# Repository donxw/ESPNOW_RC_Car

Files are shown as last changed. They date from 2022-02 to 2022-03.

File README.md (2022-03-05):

# ESPNOW_RC_Car
SMARS inspired RC Car using ESPNOW to transmit signals from the remote control unit.

*Chassis_V2 v5.f3z*

SMARS_Front2 (Small)

SMARS_Front (Small)

## Credits
This project was inspired by the SMARS arduino car described at this website:  https://www.smarsfan.com/ 

Modifications were made to use ESP based microcontrollers for RC wireless signal communication using the ESPNOW protocol. This minimized any addtional hardware by using the built in wireless capabilities of the ESP boards.  

Additionally, the wheels were redesigned to use an o-ring in place of the 3D printed tank treads.

## Libraries Used
espnow.h - here is the tutorial I used:  https://randomnerdtutorials.com/esp-now-esp8266-nodemcu-arduino-ide/
The car uses the ESP8266 commands and the Remote Control uses the ESP32 commands

No library is needed for the NodeMCU motor driver board.  The motor driver is an L293D controlled as follows:

*Motor A*
*   Direction A - Pin 0 (D3) - Boolean 0 or 1 to change direction
*   PWM A - Pin 5 (D1) - PWM 0-255 for speed

*Motor B*
*   Direction B - Pin 2 (D4) - Boolean 0 or 1 to change direction
*   PWM B - Pin 4 (D2) - PWM 0-255 for speed

## Software

### Remote Control Code: ESP32_Sender_JoystickRemote.ino

Arduino board:  ESP32 Dev Module
Code reads the joystick input and sends it to the car.

### Car Code:  NodeMCUShield_HCSR04P_RCCar_Reciever.ino

Arduino board:  NodeMCU 1.0 (ESP-12E Module)
Code recieves messages from the ESP32 and sends if forward to the motor driver to control direction and speed.  It also will beep the piezo speaker if the joystick button is pressed.  If the ultrasonic sensor detects an object in front of it, a routine backs the car up and turns it.

### MAC Address and Joystick Null 

* Program the car first (ESP8266).  Run the program and note in the serial port window what the MAC Address is.  Use this in the code for the Joystick remote control code.
* Program the remote control (ESP32).  Use the MAC address from the ESP8266.  Run the remote code and note in the serial port window the values that are being transmitted when the joystick is in the null position.
* Go back to the car code (ESP8266) and update the joystick x and y null points (valX_center, valY_center), then reprogram the car.  Turn on the joystick and watch the serial port window to assure it is recieving signals.  Tweak the null points as needed so the car is quiet when the joystick is in the neutral position.  Assure the wheels react properly to forward, back, left and right joystick.

## Hardware Used
### Car:

* ESP8266 V2.1 dev board / NodeMCU Motor Driver Shield for V2
* Good tutorial for the Shield:  https://hackaday.io/project/8856-incubator-controller/log/29291-node-mcu-motor-shield/

AliExpress:

Hardware for Car (Small)

* 2x N20 6V 200RPM-Gearmotor - https://www.ebay.com/itm/401942638877?hash=item5d95a5f11d:g:D0UAAOSw7qRdvGTe

N20Gearmotor_EBAY (Small)

* Foam double stick tape to mount motor:  https://smile.amazon.com/gp/product/B07X6D1BZL/ref=ppx_yo_dt_b_asin_title_o00_s00?ie=UTF8&psc=1
* 1/16" neoprene self stick foam for vibration isolation of motor sides.

Padding added to N20 Motors:
N20Motor_wPads (Small)

Assemble N20 Motor to chassis and attach drive wheels:
DriveWheels (Small)

Assemble idler wheels to chassis:
IdlerWheels (Small)

Add battery door and insert 9v rechargable LiPo into the chassis:
AddBattery (Small)

Add buzzer and ultrasonic sensor:
AddBuzzer UltrasonicSensor (Small)

Assemble NodeMCU and MotorDriverboard to the adapter:
AssembleCPUtoAdapter (Small)

Merge CPU adapter to chassis.  Tabs on adapter board slide into the slots on the Chassis:
MergeCPUtoChassis (Small)

For wiring, see below.

* 9V Li-ion rechargable battery:  https://smile.amazon.com/dp/B086GTFGPP?psc=1&smid=A3P4UZIS42PRQV&ref_=chk_typ_imgToDp

* 9V battery lead snap on connectors:  https://fr.aliexpress.com/item/4000015248753.html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

* O-Rings used: 3mm x 70mm ID - https://www.mcmaster.com/o-rings/width~3-000mm/
* Ultrasonic Sensor:  HC-SR04P 3.3-5v version - https://www.aliexpress.com/item/1893557869.html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

### Remote Control:

*NRF_RC_Case_ESP32 v12.f3z*

RCTransmitterCase (Small)

* Battery Shield - AliExpress:  https://www.aliexpress.com/item/4000770043723.html?spm=a2g0o.order_list.0.0.21ef18023Tfavs

BatteryShield (Small)

* Joystick - AliExpress:  https://www.aliexpress.com/item/1005003610311766.html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

Joystick

* ESP32 DevModule - AliExpress:  https://www.aliexpress.com/item/33005643254.html?spm=a2g0o.order_list.0.0.21ef1802H9bZsF

ESP32DevModule (Small)

### Wiring
ESP32 and NodeMCU pin-outs can be found here:  https://randomnerdtutorials.com/

*Car - ESP8266 NodeMCU V2*

// Ultrasonic sensor
* trigger = GPIO 10  //SD3
* echoPin = GPIO 9  //SD2
* VCC = 3.3V
* Ground = GND

// Piezo buzzer
* buzzer + = GPIO 15  //D8
* buzzer - = GND

// 9V battery
* Positive to Motor Shield Vin (Power to Arduino)
* Negative to Motor Shield Gnd
* Jumper VM to VIN (Common Power to NodeMCU and Motor)

SMARS_Top

MotorDriverBoardPinout
wiring

*RC Unit - ESP32 DevModule*

// Joystick
* Joystick Val Y = GPIO 32
* Joystick Val X = GPIO 33
* Joystick Button = GPIO 27
* Joystick +5V = 3.3v
* Joystick GND = GND

// Battery holder
* Battery 5v = Vin

WiringRCTransmitter

# 
MIT License

Copyright (c) 2022 Don Williams

Permission is hereby granted, free of charge, to any person obtaining a copy
of this software and associated documentation files (the "Software"), to deal
in the Software without restriction, including without limitation the rights
to use, copy, modify, merge, publish, distribute, sublicense, and/or sell
copies of the Software, and to permit persons to whom the Software is
furnished to do so, subject to the following conditions:

The above copyright notice and this permission notice shall be included in all
copies or substantial portions of the Software.

THE SOFTWARE IS PROVIDED "AS IS", WITHOUT WARRANTY OF ANY KIND, EXPRESS OR
IMPLIED, INCLUDING BUT NOT LIMITED TO THE WARRANTIES OF MERCHANTABILITY,
FITNESS FOR A PARTICULAR PURPOSE AND NONINFRINGEMENT. IN NO EVENT SHALL THE
AUTHORS OR COPYRIGHT HOLDERS BE LIABLE FOR ANY CLAIM, DAMAGES OR OTHER
LIABILITY, WHETHER IN AN ACTION OF CONTRACT, TORT OR OTHERWISE, ARISING FROM,
OUT OF OR IN CONNECTION WITH THE SOFTWARE OR THE USE OR OTHER DEALINGS IN THE
SOFTWARE.

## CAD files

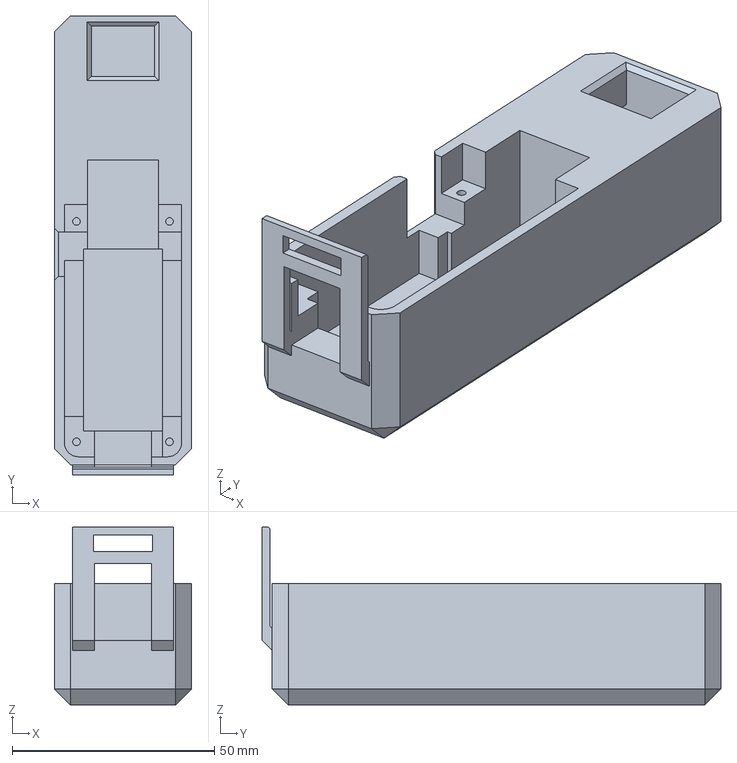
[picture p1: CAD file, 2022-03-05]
V2SetGitHub/LowerCase32.3mf
34.0 x 113.5 x 44.0 mm

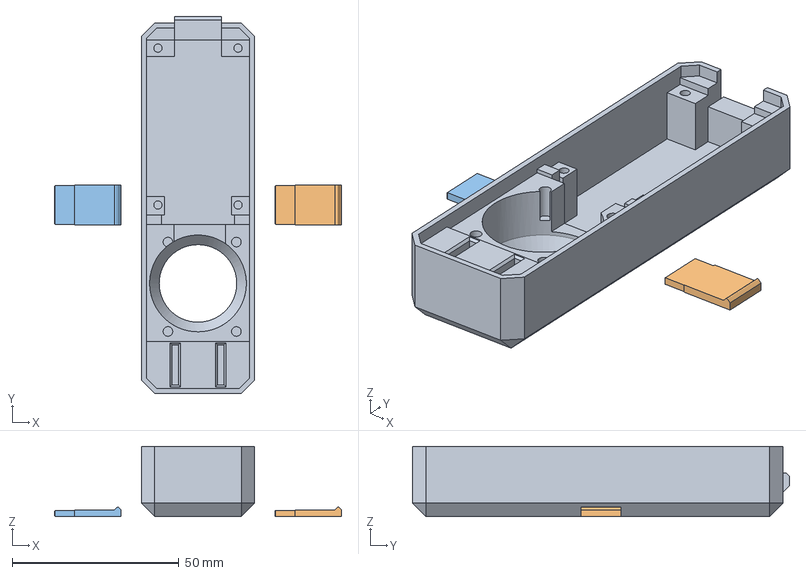
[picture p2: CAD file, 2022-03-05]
V2SetGitHub/UpperCase_ESP32_notangs.3mf
86.0 x 113.0 x 21.0 mm
UpperCase_Alt_notangs
Tang

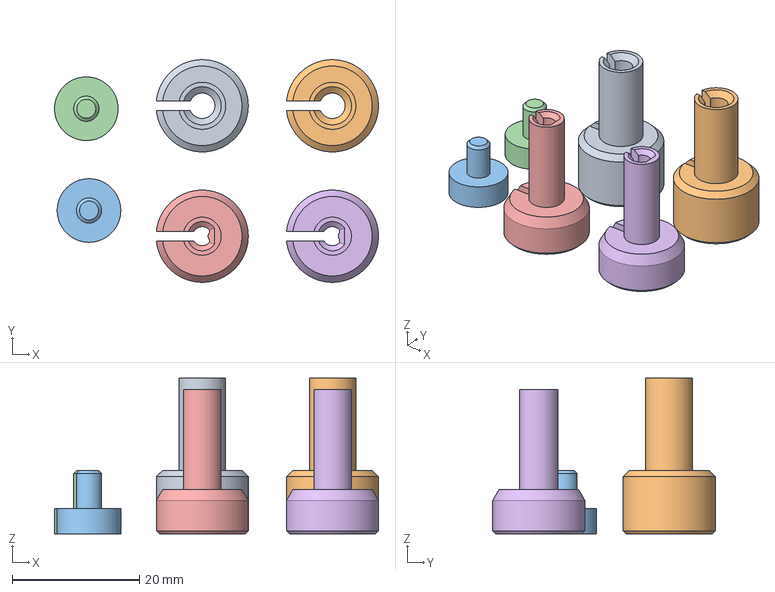
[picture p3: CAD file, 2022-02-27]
V2SetGitHub/CouplingSet.3mf
50.9 x 35.0 x 24.5 mm
Coupling x 2
CouplingStop

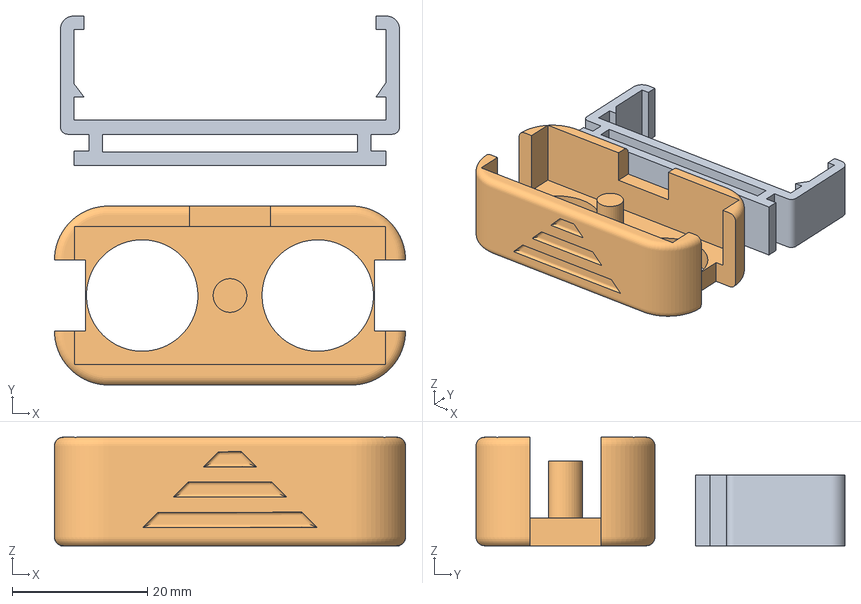
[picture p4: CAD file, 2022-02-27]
V2SetGitHub/ultrasonic_1 V1 set.3mf
52.0 x 54.6 x 16.1 mm
ultrasonic_2b v1.stl

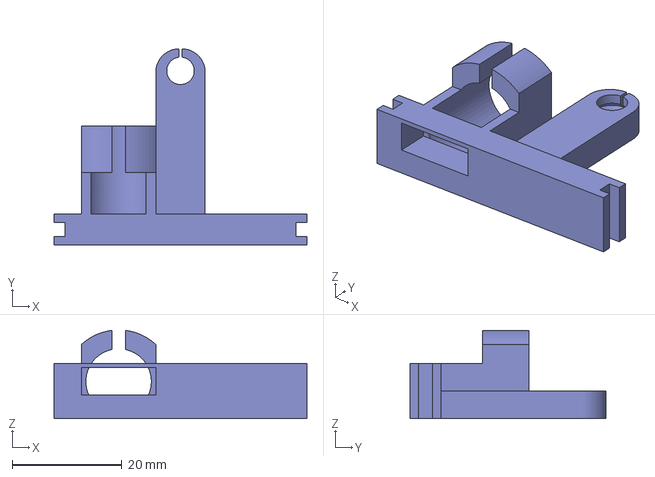
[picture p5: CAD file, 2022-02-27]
V2SetGitHub/Chassis_V1_SMARS_Buzzer&HitchAdapter_v1.3mf
46.0 x 35.7 x 16.0 mm

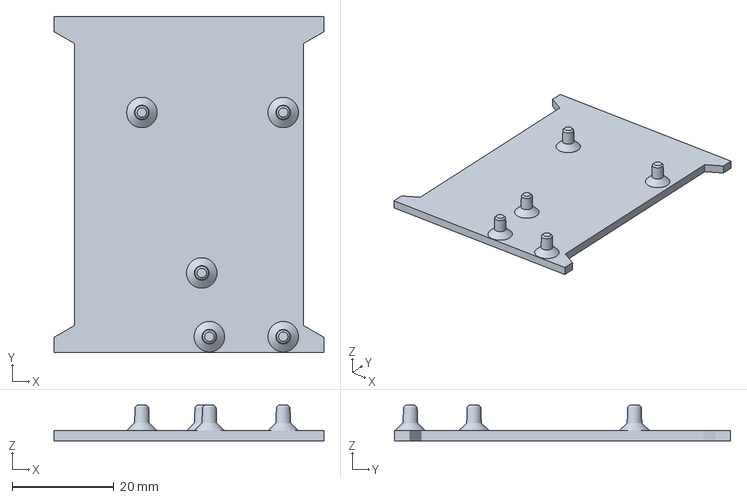
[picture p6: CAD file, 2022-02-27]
V2SetGitHub/CPUAdapterPlate.3mf
53.0 x 66.0 x 7.00 mm

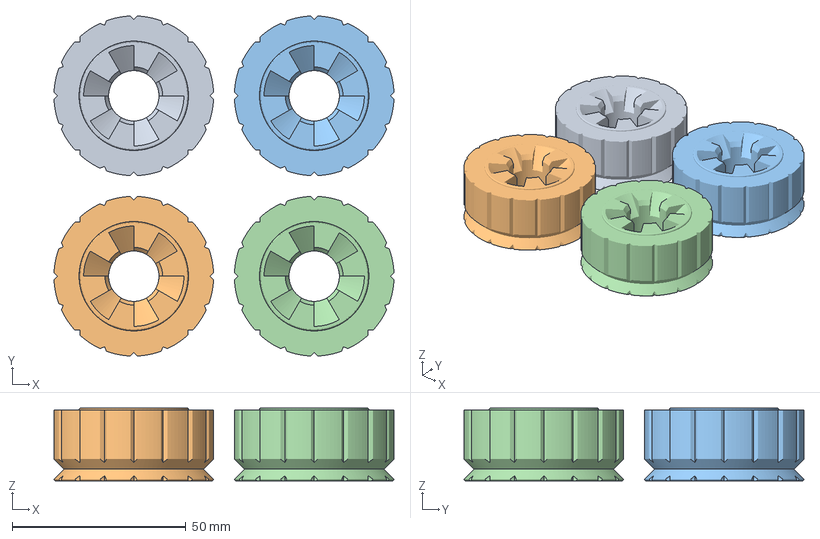
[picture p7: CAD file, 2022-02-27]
V2SetGitHub/Wheel v3 set.3mf
97.9 x 97.9 x 21.0 mm

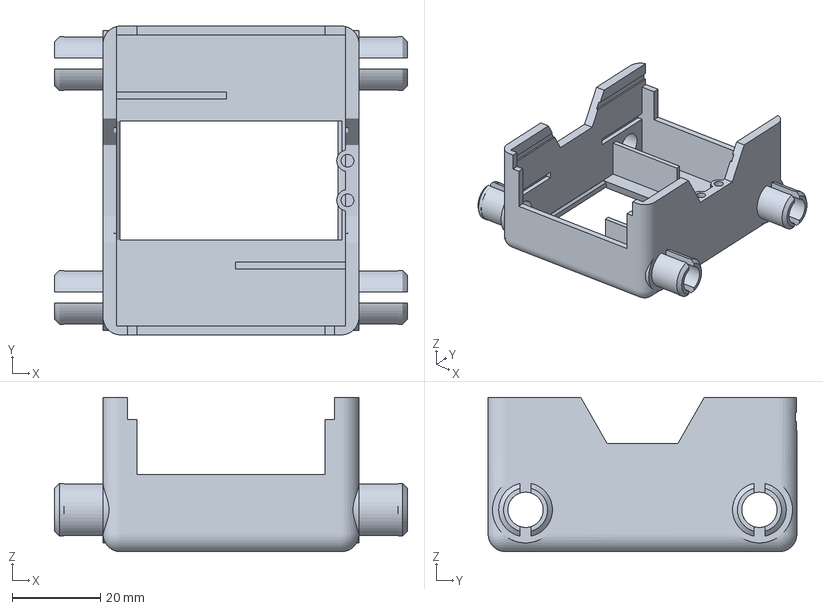
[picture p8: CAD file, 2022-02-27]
V2SetGitHub/Chassis_V2.3mf
80.0 x 70.0 x 35.0 mm

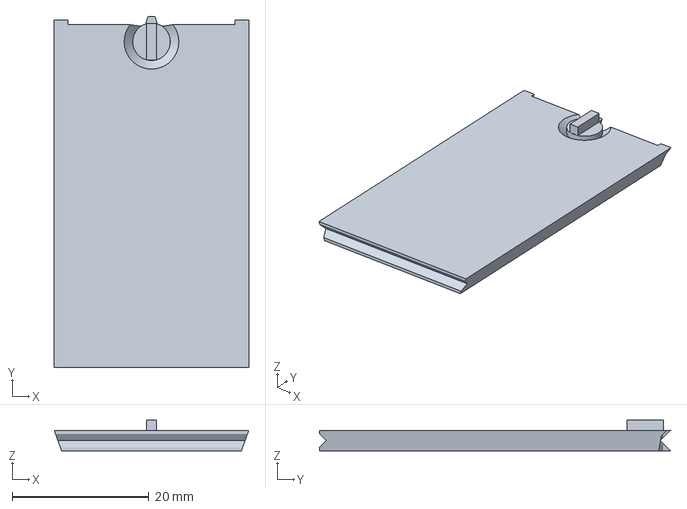
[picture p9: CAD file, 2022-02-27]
V2SetGitHub/Battery_Door v13.3mf
28.5 x 51.4 x 4.50 mm

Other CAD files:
NRF_RC_Case_ESP32 v14.f3z

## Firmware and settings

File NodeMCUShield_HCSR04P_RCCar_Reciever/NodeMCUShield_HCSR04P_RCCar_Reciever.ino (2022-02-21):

/*
    Board:  NodeMCU 1.0 (ESP-12E Module)

    Wire Motor A to left motor
    Wire Motor B to right motor
*/

#include <Arduino.h>
#include <ESP8266WiFi.h>
#include <espnow.h>
#include <Wire.h>

// Ultrasonic Sensor
#include <HCSR04.h>
// Initialize sensor to use digital pins 9 and 10.
int triggerPin = 10;
int echoPin = 9;
UltraSonicDistanceSensor distanceSensor(triggerPin, echoPin);

// Define User Types below here or use a .h file
//
#define DIRA 0  //D3
#define PWMA 5  //D1
#define DIRB 2  //D4
#define PWMB 4  //D2
#define CW 0
#define CCW 1

#define maxSpeed 255   // Max motor speed
#define deadBand 20   // Safe range to ignore round midpoint of joystick readings...
#define FORWARD 1
#define BACKWARD 2
#define LEDPIN BUILTIN_LED
// #define DEBUG

//  Global Variables
//
int dirMotorL = FORWARD;
int dirMotorR = FORWARD;
int motorSpeedL = 0;
int motorSpeedR = 0;
int speedDiff = 0;
const int valX_center = 1830;  // from testing the joystick center value
const int valY_center = 1830;
int full_range = 4095;  // full Joystick range from ESP32

typedef struct message {
  int valX;
  int valY;
  int button;
} message;

message myMessage;
bool newMessage = false;

// Define Functions below here or use other .ino or cpp files
//
void playmelody();

void onDataReceiver(uint8_t* mac, uint8_t* incomingData, uint8_t len) {
  //Serial.println("Message received.");
  newMessage = true;
  // Transform the incoming data into our message structure
  memcpy(&myMessage, incomingData, sizeof(myMessage));
}

// The setup() function runs once each time the micro-controller starts
void setup()
{
  Serial.begin(115200);

  // Setup ESPNOW
  WiFi.disconnect();
  ESP.eraseConfig();

  // Wifi STA Mode
  WiFi.mode(WIFI_STA);

  // Get Mac Add  uncomment for debug
  Serial.print("\n");
  Serial.print("Mac Address: ");
  Serial.print(WiFi.macAddress());
  Serial.println("\nESP-Now Receiver");

  // Initializing the ESP-NOW
  if (esp_now_init() != 0) {
    Serial.println("Problem during ESP-NOW init");
    return;
  }

  // Intialize ESPNow message
  myMessage.valX = valX_center;
  myMessage.valY = valY_center;
  myMessage.button = true;

  // Set ESPNow Role
  //esp_now_set_self_role(ESP_NOW_ROLE_SLAVE);
  //
  // Register the receiver callback function
  esp_now_register_recv_cb(onDataReceiver);

  // Setup Motor Sheild Pins
  pinMode(DIRA, OUTPUT);
  pinMode(PWMA, OUTPUT);
  pinMode(DIRB, OUTPUT);
  pinMode(PWMB, OUTPUT);

  // Play tone on power up
  playmelody();

  // turn on built in LED
  pinMode(LEDPIN, OUTPUT);
  digitalWrite(LEDPIN, LOW);
    
#ifdef DEBUG
  // plotter logo
  Serial.print(" ValY ValX Button ");
#endif // DEBUG
    
  //test ESPNOW messaging
  //myMessage.valY = 3000;
}

// Add the main program code into the continuous loop() function
void loop()
{
  // ultrasonic sensor
  double distance = distanceSensor.measureDistanceCm();
  // send sensor readings to serial port 
  //Serial.print("Distance (cm):  "); Serial.println(distance);
  
  // take action if object is detected  
  if (distance <= 20) {
    if (distance != -1) {  // ignore bad readings

      // move backward 1 sec
      digitalWrite(DIRA, CW);  //Left Motor CW for Reverse
      analogWrite(PWMA, maxSpeed);
      digitalWrite(DIRB, CCW);  //Right Motor CCW for Reverse
      analogWrite(PWMB, maxSpeed);
      delay(1000);

      // turn 0.7 sec
      digitalWrite(DIRA, CW);  //Left Motor CW for Reverse
      analogWrite(PWMA, maxSpeed);
      digitalWrite(DIRB, CW);  //Right Motor CCW for Reverse
      analogWrite(PWMB, maxSpeed);
      delay(700);  // adjust until ~180 turn is achieved
    }
  }

  // uncomment define DEBUG to run
#ifdef DEBUG
  if (newMessage == true) {
    Serial.print(myMessage.valY); Serial.print(" ");
    Serial.print(myMessage.valX); Serial.print(" ");
    Serial.print(myMessage.button * 1000); Serial.print("\n");
    newMessage = false;
  }
#endif // DEBUG
    
  // map joystick Y-axis to motor speed (deadband may not be needed since accounted for in sender)
  motorSpeedL = motorSpeedR = 0;
  if (myMessage.valY < (valY_center - deadBand)) {
    motorSpeedL = map(myMessage.valY, 0, valY_center, -maxSpeed, 0);
    motorSpeedR = motorSpeedL;
  }
  else if (myMessage.valY > (valY_center + deadBand)) {
    motorSpeedL = map(myMessage.valY, valY_center, full_range, 0, maxSpeed);
    motorSpeedR = motorSpeedL;
  }

  // determine speed difference in motors from joystick X-axis value
  speedDiff = 0;
  if (myMessage.valX < valX_center - deadBand) {
    speedDiff = map(myMessage.valX, 0, valX_center, -maxSpeed, 0);
  }
  else if (myMessage.valX > valX_center + deadBand) {
    speedDiff = map(myMessage.valX, valX_center, full_range, 0, maxSpeed);
  }

  // set Motor Speeds
  motorSpeedL += speedDiff;
  motorSpeedR -= speedDiff;

  dirMotorL = motorSpeedL < 0 ? BACKWARD : FORWARD;  //LEFT MOTOR_CH_A CCW IS FORWARD
  dirMotorR = motorSpeedR < 0 ? BACKWARD : FORWARD;  //RIGHT MOTOR_CH_B CW IS FORWARD

  // limit Motor Speeds to max value allowed
  motorSpeedL = abs(motorSpeedL);
  motorSpeedR = abs(motorSpeedR);
  if (motorSpeedL > maxSpeed) motorSpeedL = maxSpeed;
  if (motorSpeedR > maxSpeed) motorSpeedR = maxSpeed;

  // set Left motor speed & direction
  //dirMotorL == FORWARD ? M1.setmotor(_CCW, motorSpeedL) : M1.setmotor(_CW, motorSpeedL);
  if (dirMotorL == FORWARD) {
    digitalWrite(DIRA, CCW);  //Left Motor CCW for Forward
    analogWrite(PWMA, motorSpeedL);
  }
  else {
    digitalWrite(DIRA, CW);  //Left Motor CW for Reverse
    analogWrite(PWMA, motorSpeedL);
  }

  // set Right motor speed & direction
  //dirMotorR == FORWARD ? M2.setmotor(_CW, motorSpeedR) : M2.setmotor(_CCW, motorSpeedR);
  if (dirMotorR == FORWARD) {
    digitalWrite(DIRB, CW);  //Right Motor CW for Forward
    analogWrite(PWMB, motorSpeedR);
  }
  else {
    digitalWrite(DIRB, CCW);  //Right Motor CCW for Reverse
    analogWrite(PWMB, motorSpeedR);
  }

  // beep on button push
  if (myMessage.button == false) {
    playmelody();
    Serial.println("beep beep");
    myMessage.button = true;
  }

  delay(100); //update @ 20Hz

}

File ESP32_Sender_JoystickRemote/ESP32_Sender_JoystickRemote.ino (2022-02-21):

/**
   ESP-NOW: ESP32 Broadcast with ESP-Now
   Use Get_MAC.ino to get the MAC address of the CPU to send the joystick data to
   ESP32 has a 12 bit ADC 0 to 4095 steps

   board:  ESP32 Dev Module

   Pin assignments:
    GPIO 32 - valY
    GPIO 33 - valX
    GPIO 27 - joystick button

*/
#include <Arduino.h>
#include <WiFi.h>
#include <esp_now.h>

//ESP8266 Mac address (first peer)
//30:83:98:B1:DA:0D Red Car 1 NodeMCU MAC
uint8_t mac_peer1[] = {0x30, 0x83, 0x98, 0xB1, 0xDA, 0x0D};

esp_now_peer_info_t peer1;

// Pins
#define BTN 27
#define VRY 33
#define VRX 32

// Variables
int state = 0;
const int valX_center = 1860;  // from testing the joystick center value
const int valY_center = 1826;
const int deadBand = 20;
int deltaX = 0;
int deltaY = 0;
int prev_deltaX = 1000;
int prev_deltaY = 1000;

// Structured variable to be sent by ESPNOW
typedef struct message {
  int valX;  // left - right joystick
  int valY;  // fwd - back joystick
  bool button;  // button state
};
struct message myMessage;

// Callback when data is sent
void OnDataSent(const uint8_t *mac_addr, esp_now_send_status_t status) {
  Serial.print("\r\nLast Packet Send Status:\t");
  Serial.println(status == ESP_NOW_SEND_SUCCESS ? "Delivery Success" : "Delivery Fail");
}

void setup() {
  Serial.begin(115200);
  WiFi.mode(WIFI_STA);

  // Get Mac Add
  Serial.print("Mac Address: ");
  Serial.print(WiFi.macAddress());
  Serial.println("ESP32 ESP-Now Broadcast");

  // Initializing the ESP-NOW
  if (esp_now_init() != 0) {
    Serial.println("Problem during ESP-NOW init");
    return;
  }

  memcpy(peer1.peer_addr, mac_peer1, 6);
  peer1.channel = 0;
  // Register the peer
  Serial.println("Registering a peer 1");
  if ( esp_now_add_peer(&peer1) == ESP_OK) {
    Serial.println("Peer 1 added");
  }

  esp_now_register_send_cb(OnDataSent);

  pinMode(BTN, INPUT_PULLUP);  // joystick button grounds the pin
}

void loop() {

  deltaY = abs(analogRead(VRY) - valY_center);
  deltaX = abs(analogRead(VRX) - valX_center);

  deltaY = deltaY < deadBand ? 0 : deltaY;  // if deltaY is less than deadband, set to zero, else no change
  deltaX = deltaX < deadBand ? 0 : deltaX;

  if (deltaY != prev_deltaY || deltaX != prev_deltaX ) {
    prev_deltaY = deltaY;
    prev_deltaX = deltaX;
    myMessage.valY = analogRead(VRY);
    myMessage.valX = analogRead(VRX);
    Serial.printf("valY: %i", myMessage.valY);
    Serial.printf(", valX: %i\n", myMessage.valX);
    state = digitalRead(BTN);
    myMessage.button = state;
    esp_now_send(NULL, (uint8_t *) &myMessage, sizeof(myMessage));
  }

  if (state != digitalRead(BTN)) {
    myMessage.valY = analogRead(VRY);
    myMessage.valX = analogRead(VRX);
    state = digitalRead(BTN);
    myMessage.button = state;
    esp_now_send(NULL, (uint8_t *) &myMessage, sizeof(myMessage));
  }

  delay(100);  // run at 10 Hz
}
